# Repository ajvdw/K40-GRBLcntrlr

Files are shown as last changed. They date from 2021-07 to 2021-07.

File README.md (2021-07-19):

# K40 GRBL cntrlr
 K40 ESP32 GRBL Controller.
 
This is a replacement for the M2 Nano controller. 
It supports GRBL 1.1 and raster engraving with grayscales.
Since the controller is based on ESP32 it supports Serial, Bluetooth and Wifi communications as well as working offline through the use of an SDCard. 
Designed with DIY in mind, all through-hole components or through-hole modules.

Firmware is forked from https://github.com/bdring/Grbl_Esp32, I only added a machine definition to it. Instructions how to build the software can be found there as well.

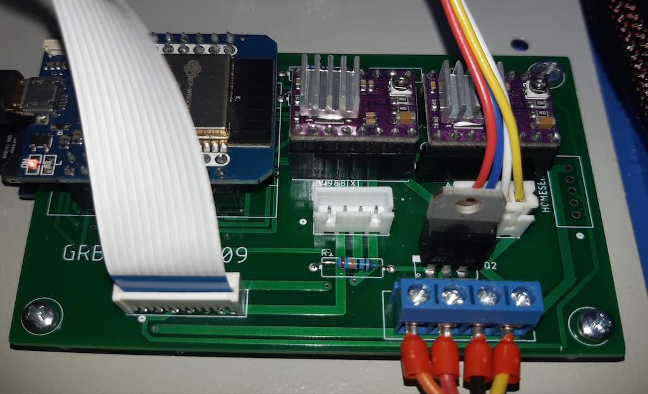
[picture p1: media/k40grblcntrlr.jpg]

K40 GRBLCNTRLR v0.9 in situ.

## B.O.M.

- 1x PCB
- 1x Ttgo Wemos Mini D1 ESP32 Wifi + Bluetooth CP2104 Module
- 2x StepStick DRV8825 or A4988
- 2x resistor 4K7 1/4W
- 1x resistor 100K 1/4W
- 2x elect.cap. 47uF 36V
- 1x MOSFET N-Channel p75nf75 (similar to TO220)
- 1x 1.25Mm Ffc/Fpc Connector 12P
- 2x JST XH2.54 4P 
- 1x JST XH2.54 5P 
- 1x Micro Sd Tf Card Memory Shield Module SPI for Arduino 3.3V
- 1x Term.conn 5.1mm 4P

Total cost should be less than 20$.

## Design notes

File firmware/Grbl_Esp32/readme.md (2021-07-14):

# Grbl_Esp32

Cloned from https://github.com/bdring/Grbl_Esp32.

Follow the build instructions, version critial!

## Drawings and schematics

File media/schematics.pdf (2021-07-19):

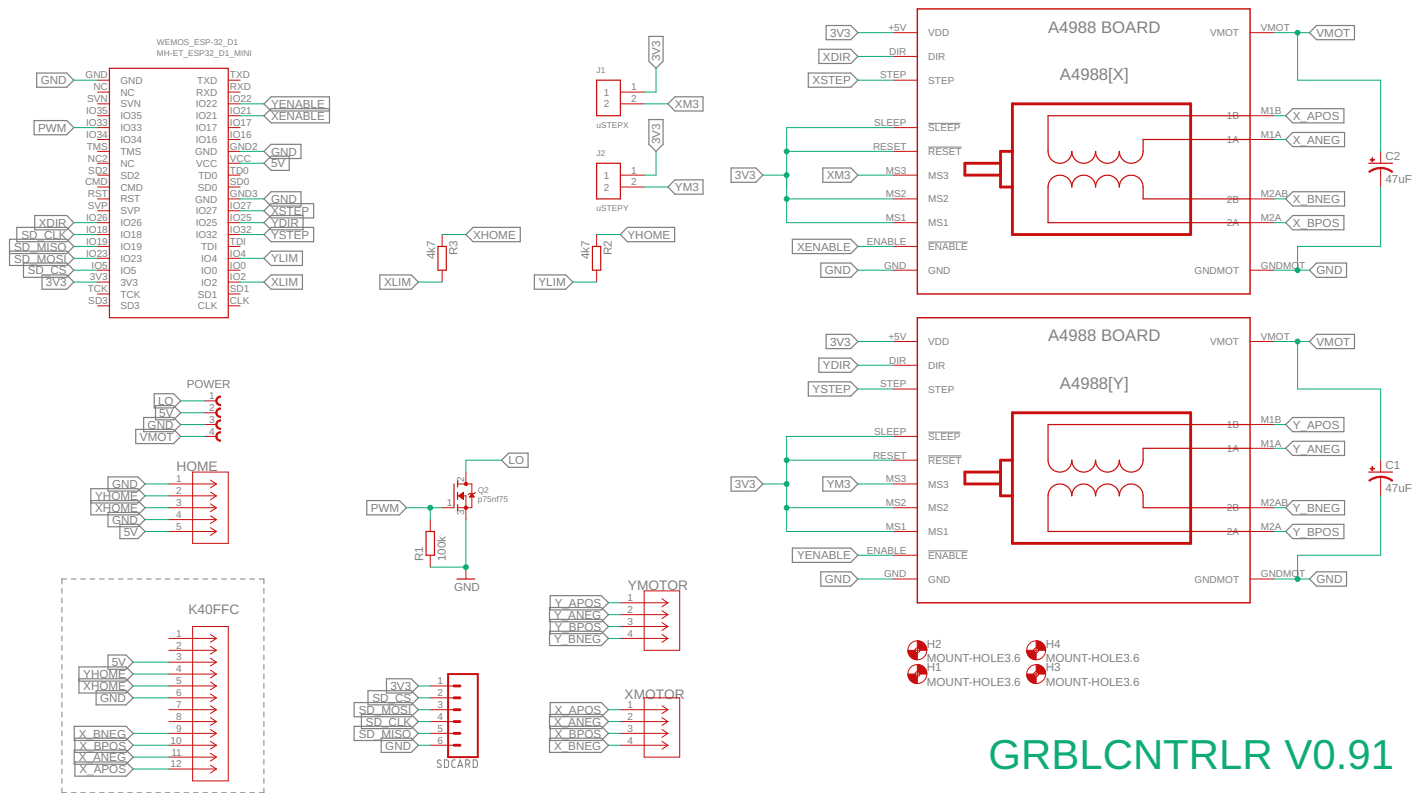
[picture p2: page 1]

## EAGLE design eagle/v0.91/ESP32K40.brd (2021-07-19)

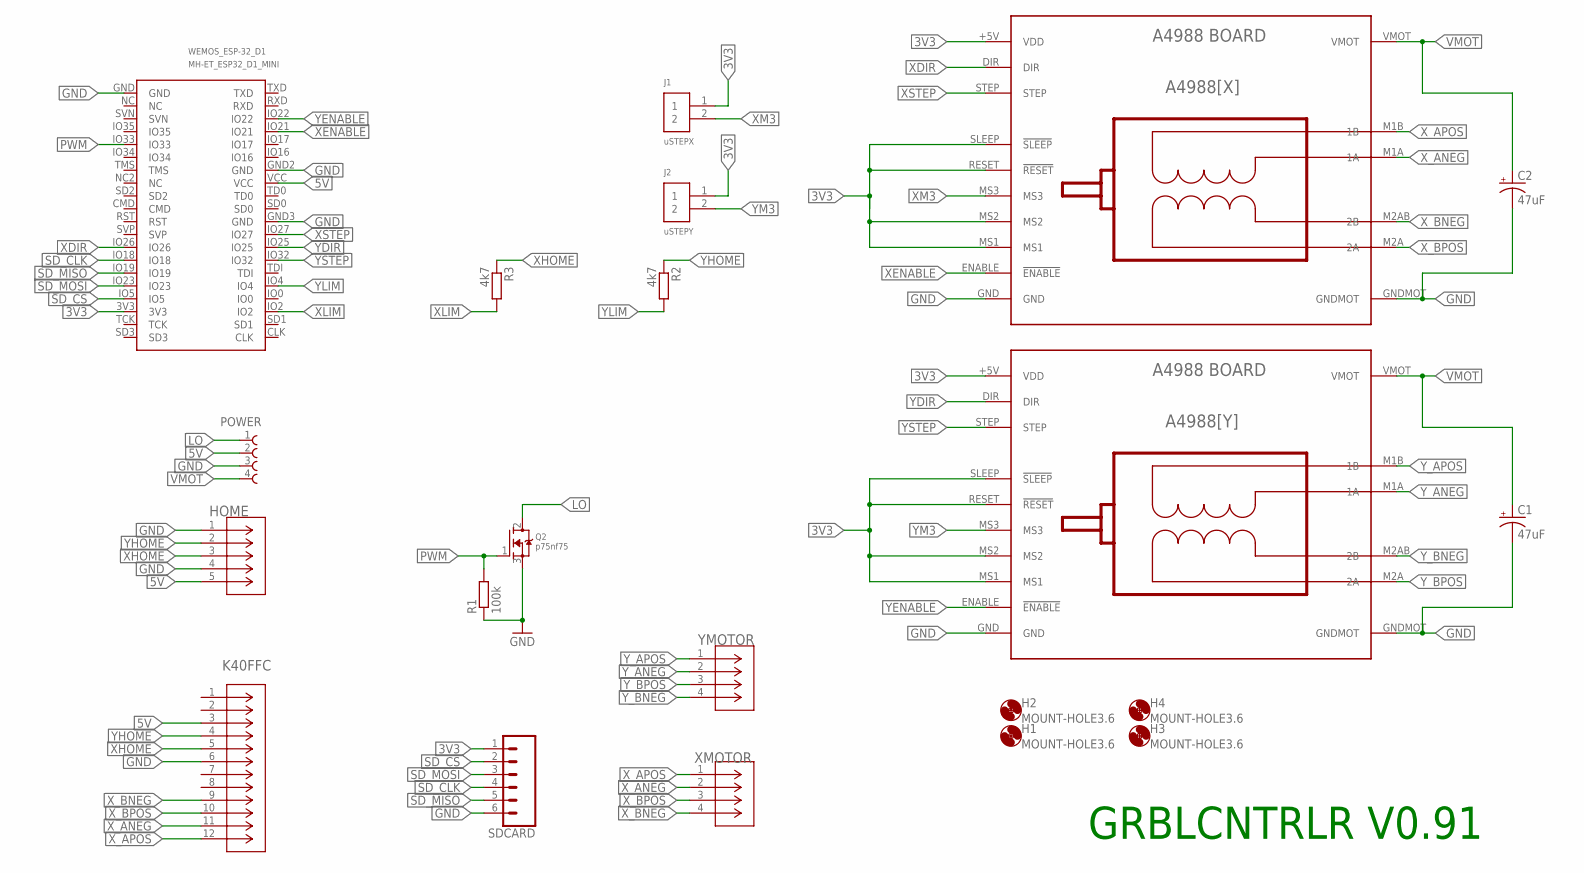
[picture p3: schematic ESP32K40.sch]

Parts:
A4988[X]: XMOTOR; BOARD_A4988
A4988[Y]: YMOTOR; BOARD_A4988
C1, C2: 47uF; TAP5-70
H1, H2, H3, H4: MOUNT-HOLE3.6; 3,6
HOME: B5B-XH-A(LF)(SN); CONN_B5B-XH-A(LF)(SN)_JST
J1: uSTEPX; 61300211121
J2: uSTEPY; 61300211121
K40FFC: 1-84534-2; CON12_TH_FCC-FPC2
POWER: 691371700004B
Q2: p75nf75; TO220V
R1: 100k; V234/12
R2, R3: 4k7; V234/12
SDCARD: CONN_06LONGPADS; 1X06_LONGPADS
WEMOS_ESP-32_D1: MH-ET_ESP32_D1_MINI
XMOTOR: B4B-XH-A_(LF)(SN); CONN_B4B-XH-A_(LF)(SN)_JST
YMOTOR: B4B-XH-A_(LF)(SN); CONN_B4B-XH-A_(LF)(SN)_JST

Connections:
3V3: A4988[X].+5V (VDD), A4988[X].MS1, A4988[X].MS2, A4988[X].RESET (!RESET), A4988[X].SLEEP (!SLEEP), A4988[Y].+5V (VDD), A4988[Y].MS1, A4988[Y].MS2, A4988[Y].RESET (!RESET), A4988[Y].SLEEP (!SLEEP), J1.1, J2.1, SDCARD.1, WEMOS_ESP-32_D1.3V3
5V: HOME.5, K40FFC.3, POWER.2, WEMOS_ESP-32_D1.VCC
GND: A4988[X].GND, A4988[X].GNDMOT, A4988[Y].GND, A4988[Y].GNDMOT, C1.-, C2.-, HOME.1, HOME.4, K40FFC.6, POWER.3, Q2.3 (S), R1.1, SDCARD.6, WEMOS_ESP-32_D1.GND, WEMOS_ESP-32_D1.GND2 (GND), WEMOS_ESP-32_D1.GND3 (GND)
LO: POWER.1, Q2.2 (D)
PWM: Q2.1 (G), R1.2, WEMOS_ESP-32_D1.IO33
SD_CLK: SDCARD.4, WEMOS_ESP-32_D1.IO18
SD_CS: SDCARD.2, WEMOS_ESP-32_D1.IO5
SD_MISO: SDCARD.5, WEMOS_ESP-32_D1.IO19
SD_MOSI: SDCARD.3, WEMOS_ESP-32_D1.IO23
VMOT: A4988[X].VMOT, A4988[Y].VMOT, C1.+, C2.+, POWER.4
XDIR: A4988[X].DIR, WEMOS_ESP-32_D1.IO26
XENABLE: A4988[X].ENABLE (!ENABLE), WEMOS_ESP-32_D1.IO21
XHOME: HOME.3, K40FFC.5, R3.1
XLIM: R3.2, WEMOS_ESP-32_D1.IO2
XM3: A4988[X].MS3, J1.2
XSTEP: A4988[X].STEP, WEMOS_ESP-32_D1.IO27
X_ANEG: A4988[X].M1A (1A), K40FFC.11, XMOTOR.2
X_APOS: A4988[X].M1B (1B), K40FFC.12, XMOTOR.1
X_BNEG: A4988[X].M2AB (2B), K40FFC.9, XMOTOR.4
X_BPOS: A4988[X].M2A (2A), K40FFC.10, XMOTOR.3
YDIR: A4988[Y].DIR, WEMOS_ESP-32_D1.IO25
YENABLE: A4988[Y].ENABLE (!ENABLE), WEMOS_ESP-32_D1.IO22
YHOME: HOME.2, K40FFC.4, R2.1
YLIM: R2.2, WEMOS_ESP-32_D1.IO4
YM3: A4988[Y].MS3, J2.2
YSTEP: A4988[Y].STEP, WEMOS_ESP-32_D1.IO32
Y_ANEG: A4988[Y].M1A (1A), YMOTOR.2
Y_APOS: A4988[Y].M1B (1B), YMOTOR.1
Y_BNEG: A4988[Y].M2AB (2B), YMOTOR.4
Y_BPOS: A4988[Y].M2A (2A), YMOTOR.3

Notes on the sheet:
GRBLCNTRLR V0.91

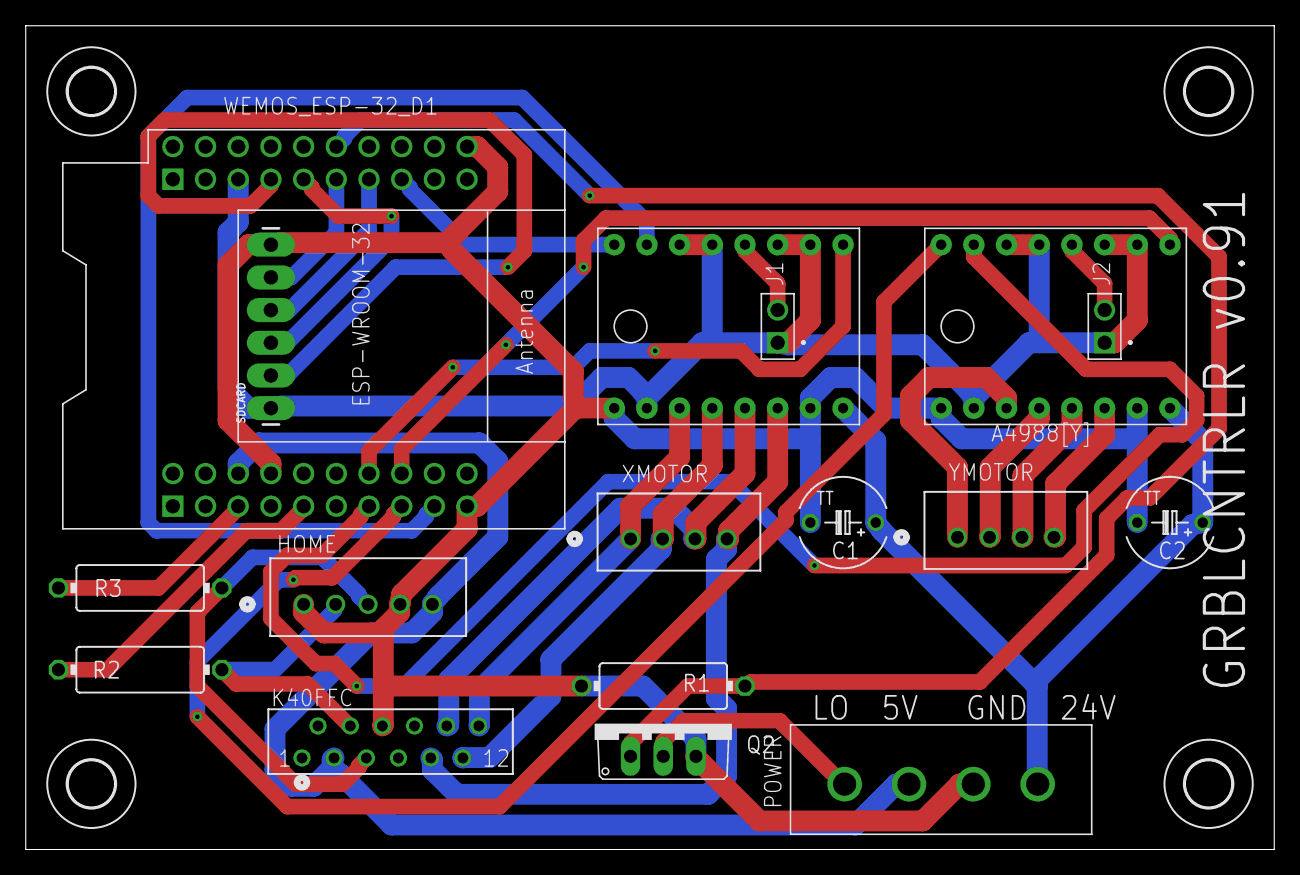
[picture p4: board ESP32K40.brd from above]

Board: 2 copper layers, 97.0 x 64.0 mm, 21 parts (0 on the bottom side), 30 nets.

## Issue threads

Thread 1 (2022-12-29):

Photo not matching board

Rad3d21, 2022-12-29:
Nice clean and simple board. Great ! Most things are straightforward but not everything.
The photo does not match the current gerber file. The homeser on the right is not there anymore.
This is also the jst 5pin mentioned in the BOM I guess.
Another thing described is sdcard reader but nowhere shown how this is connected.
Could you please elaborate some more ?

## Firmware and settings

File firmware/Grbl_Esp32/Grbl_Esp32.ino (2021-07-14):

/*
  Grbl_ESP32.ino - Header for system level commands and real-time processes
  Part of Grbl
  Copyright (c) 2014-2016 Sungeun K. Jeon for Gnea Research LLC

	2018 -	Bart Dring This file was modified for use on the ESP32
					CPU. Do not use this with Grbl for atMega328P

  Grbl is free software: you can redistribute it and/or modify
  it under the terms of the GNU General Public License as published by
  the Free Software Foundation, either version 3 of the License, or
  (at your option) any later version.
  Grbl is distributed in the hope that it will be useful,
  but WITHOUT ANY WARRANTY; without even the implied warranty of
  MERCHANTABILITY or FITNESS FOR A PARTICULAR PURPOSE.  See the
  GNU General Public License for more details.
  You should have received a copy of the GNU General Public License
  along with Grbl.  If not, see <http://www.gnu.org/licenses/>.
*/

#include "src/Grbl.h"

void setup() {
    grbl_init();
}

void loop() {
    run_once();
}

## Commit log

2021-07-14 Initial version
    [ESP32K40.brd, ESP32K40.sch]
2021-07-19 proper mosfet type
    [ESP32K40.brd, ESP32K40.sch]
2021-07-19 changed mosfet type

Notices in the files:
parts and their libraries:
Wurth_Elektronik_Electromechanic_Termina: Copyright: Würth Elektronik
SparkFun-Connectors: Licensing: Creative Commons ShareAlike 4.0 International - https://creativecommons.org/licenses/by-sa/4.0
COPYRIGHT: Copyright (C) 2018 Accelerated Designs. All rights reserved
